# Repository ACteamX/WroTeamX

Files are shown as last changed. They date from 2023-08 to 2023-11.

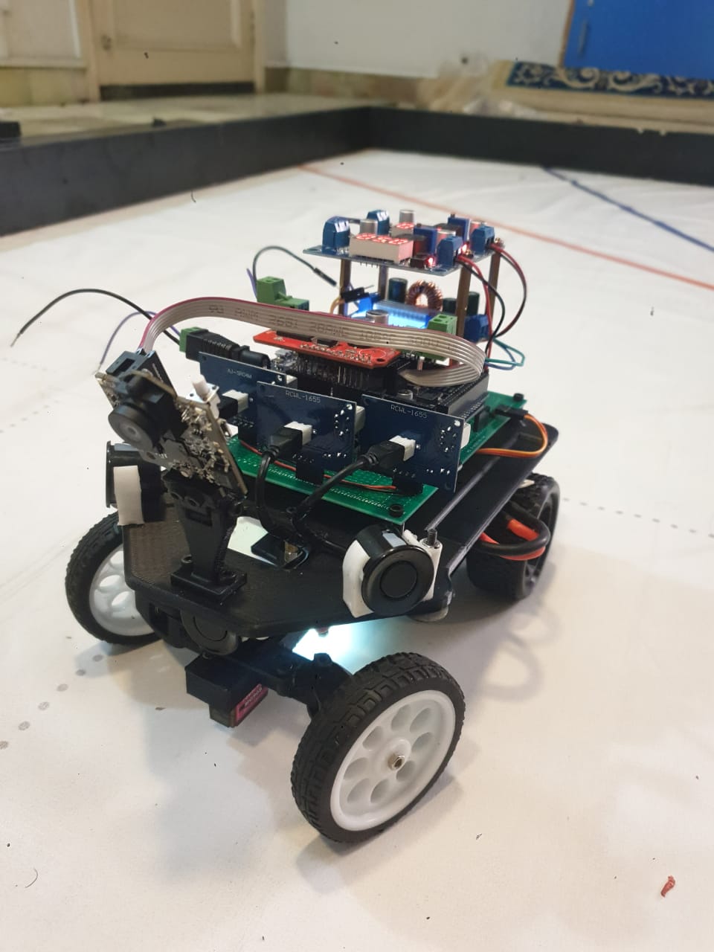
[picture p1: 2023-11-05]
v-photos/new design/wro (11).jpg

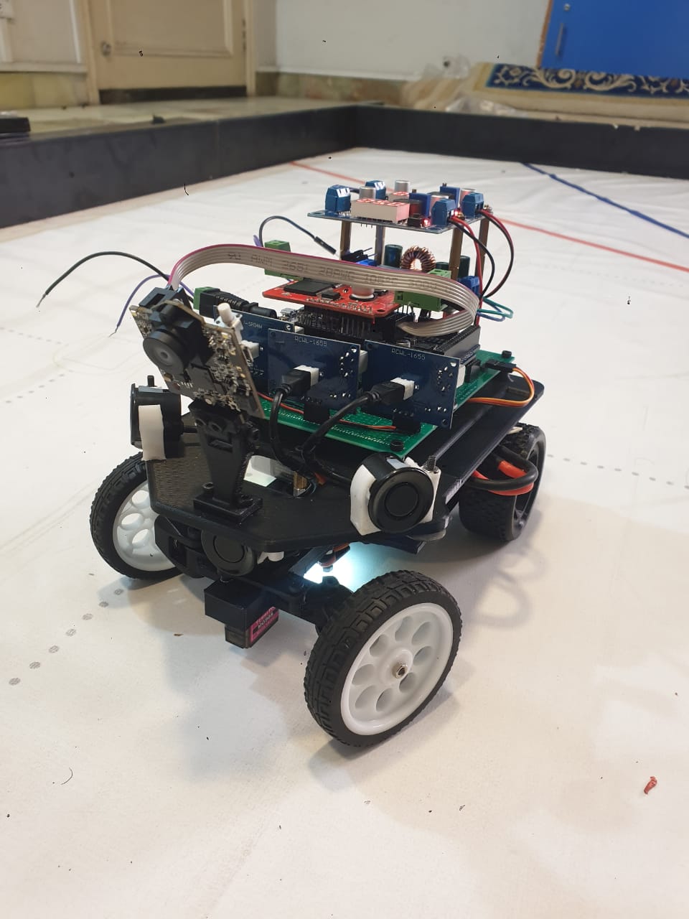
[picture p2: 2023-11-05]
v-photos/new design/wro (13).jpg

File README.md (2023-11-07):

# WroTeamX

This repository contains technical materials for a self-navigating vehicle prototype intended for the WRO Future Engineers event in the 2023 season. Detailed insights into each subcomponent of the robotic system can be explored in the README.md files located within respective folders.

### Contents:

- **Build:** Detailed documentation focusing on our chassis design and the rationale behind the chosen materials.
- 
- **Electrical:** Schematic diagrams illustrating the interconnections among various electromechanical components, including datasheets and explanations for component selection.
- 
- **Models:** Files used by 3D printers to fabricate the vehicle's components.
- 
- **t-Photos:** Folder containing team photos.
- 
- **v-Photos:** Images of the robot.
- 
- **Src:** Software code responsible for controlling all the components programmed for the competition.
- 
- **Schemes:** Documentation and diagrams elucidating our approach to solving the competition's challenges.
- 
- **Video:** Includes the 'video.md' file containing the link to a video demonstrating the vehicle's operational abilities.

### Requirements:

This project meets the following requirements specified by the WRO Future Engineers event:
**Mobility Management** is found in electrical and models

**Power and Sense Management** is found in schemes.

***Components List** The list of all components is in schemes as well.

**Obstacle Management** and coding files are found in src.

**Pictures**  Team and Vehicle is found in photos.

**Performance Videos** are in video folder.

**Engineering Factor** is found in models.

### Introduction:
AcTeamX by mechabotix is a team of high school students from Aitchison College Lahore Pakistan. We have been working on our robot since june .
We have won the National round and then qualified for international round. We are working hard to get the position in the International round as well.
Instead of buying OFF THE SHELF materials for the design of our car , we have designed our car by ourselves . We made 3d models then got the print of the car .
In the National round , we made a design and used that oe but that was really big car and we afraid that it may hit the obstacles so we changed the design making it smaller one .
As far as the electrical components are concerned , we have used pixy camera for detecting the obstacles and used sonar sensors for avoiding the walls .

### Aim of participation:

**Skills Enhancement:** Develop expertise in robotics, coding, and problem-solving.

**Innovative Solutions:** Foster creativity in tackling challenges through innovative robotics solutions.

**Team Collaboration:** Strengthen teamwork and communication skills within a competitive environment.

**Global Engagement:** Engage and learn from a diverse global community of robotics enthusiasts.

**Critical Thinking:** Enhance critical thinking and problem-solving abilities in real-world scenarios.

**Competition Experience:** Learn to perform under pressure and manage time effectively in a competitive setting.

**STEM Advocacy:** Promote STEM education and interest in robotics and technology.

**Personal Growth:** Encourage individual growth and confidence through overcoming challenges.

**Technology Exposure:** Stay updated on cutting-edge technology trends in robotics and automation.

**NEW CAR VS OLD CAR**
NEW DESIGN) sidetiltright

**DIFFERENCES**

**1.DESIGN**

  **OLD CAR** We made a bigger car in National round for WRO and we have won too but we felt that it is too big to cross obstacles .
We were afraid that it might hit the obstacles with its big design.the dimensions of our old car are 26x19.8x25cm length width and height and the weight of this car was 1490g. Our old car was very close to maximum dimensions are weight allowed for the car so we had a concern of disqualification as well. We used thick 3D printed wheels as well in our old car. We used some 3d printed parts and used some PVC sheets for the upper base of our car , it was 3 storeys car which was very big so we decided to change it.

**NEW CAR** In the new car , we made a new design making it small and fast. We have made so many changes in our design. The new dimensions are very less than the dimensions of our prevoius robot.This Robot is fast and we have have made design flexible that we can easily change the components when required. 

**ELECTRONICS components**

**Old Car** In the old car, we used the raspberry pi and connected it with arduino by sending signals to arduino from pi and we used CV2 library for detecting the obstacles.We used Power banks to power our arduino and raspberry pi. Also, we used only two buck and boost convertors for powering the main motor , sensors and servo motor. This thing disturbed us so much that whenever servo motor moves that it produces noise in the sensors and readings fluatuates.So, we have faced so many issues in our old robot .

**New Car** In the new car, we have used Arduino due and for obstacle detetction we have used the pixy camera as it is easy to use and train models. For reducing noise, we have now used two batteries and 1 battery is connected in parallel with one buck convertor(giving 5V to sensors) and one buck-boost convertor(giving power to drive motor and Arduino Due), the other battery is connected with a convertor separately which is giving 5V to servo motor. Also for making the output smooth , we have used some capacitors in parallel fashion to all our components like sensors, motors etc.
So, these are the thing which we missing in our prevois Robot.

ALSO,
we have used vero board and designed the circuit on it as it looks professional and accurate , it was not present in old robot.

vero board
vero board

**Note**

****An important thing to note that is that we tried to use MPU920 and RGB color sensor for getting the best output but the sensors available in Pakistan are too noisy to use, we tried so many times for getting accurate readings but failed, with MPU920 we used kalman filter and it was working fine but when we tried to put it in our car then the readings started fluctuating and same faced same thing with RGB color sensor, so we tried to rely on encoder motor and pixy camera for making U-turn.
we have uploaded our all codes in the SRC file.**

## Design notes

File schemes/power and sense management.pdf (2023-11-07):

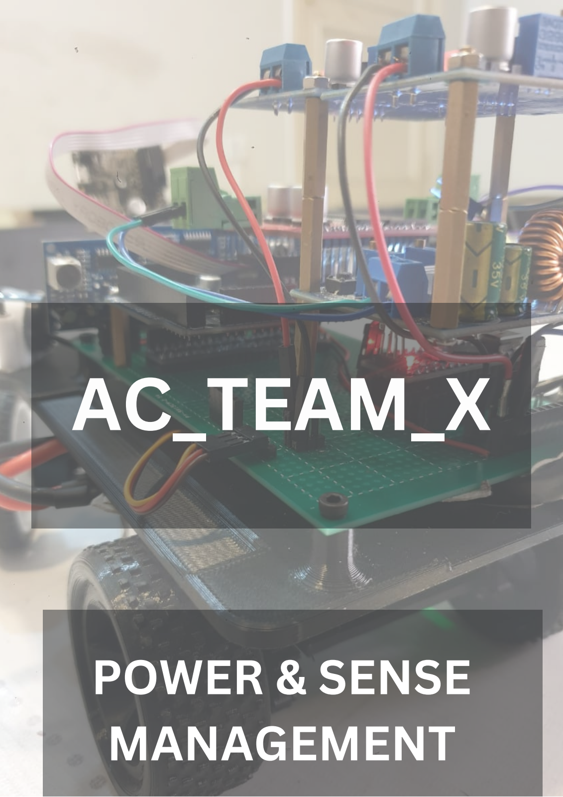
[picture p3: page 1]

AC

_

# TEAM

_

X

# POWER & SENSE MANAGEMENT

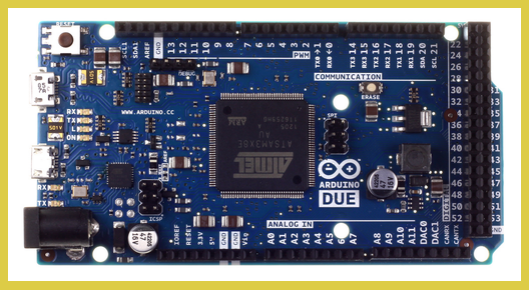
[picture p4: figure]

ARDUINO
DUE

1.

### Instead of using Arduino mega, we have preferred using Arduino Due because of its performance. The RAM and ROM of Arduino

Due is way ahead than Arduino mega .

### The processor of due is also good than Arduino mega . So using Arduino due will give

us a good result.

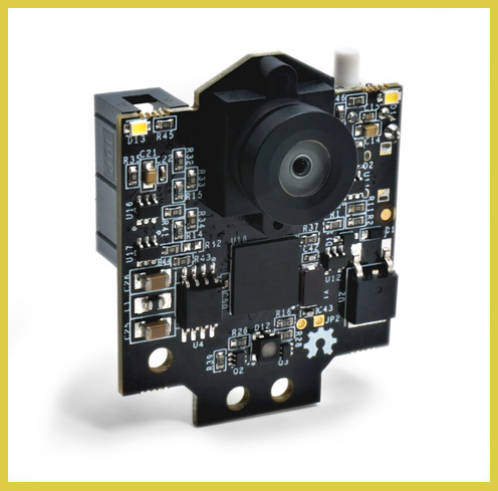
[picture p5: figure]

2.

Pixy Camera, is a compact and versatile vision system primarily used for object recognition and tracking in robotics and automation. Its primary function revolves around efficient object detection and recognition, making it a popular choice for obstacle detection applications . The best thing about pixy is that we can train the models easily and it is a flexible camera . We are detecting green and red colors and sending signal to Arduino . We may use it for detecting blue color and making a U-turn.

### PIXY CAMERA

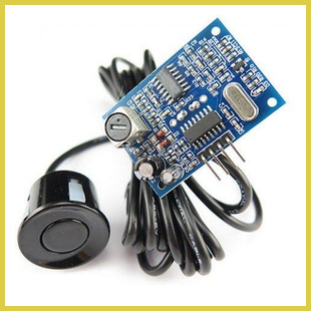
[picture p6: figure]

7.

JSN SR04T
Water Proof
Ultrasonic
Sensor

8

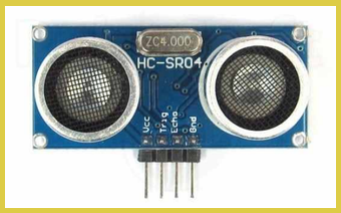
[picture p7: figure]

If necessary , we will use this sonar sensor for our critical turns like where the distance is less than 10cm and we have to avoid the robot from hitting walls . The JSON sonar can’t measure distance below 20cm. So, after testing we will final whether or not we are using the simple sonar sensors .

HC-SR04
Ultrasonic
Sensor

"Jason Waterproof Sonar Sensors" are cutting-edge sensors engineered for obstacle avoidance in autonomous vehicles, renowned for their precision and reliability. These sensors, utilizing sonar technology, offer accurate distance measurement and object detection. Resilient and durable, they ensure consistent and precise readings in varied conditions. We are using 3 of these sensors and we have made a sensor holder too .

# SENSORS AND BOARD

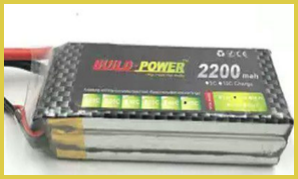
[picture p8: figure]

### 9. We are using one 2200mAh battery and one 1300mAh

battery in our robot .
we faced so many issues of servo motor noise so we are giving power to our servo motor with a separate lipo battery now. The big lipo battery is dedicated for our drive motor , arduino due and all the sensors .

Lipo
Battery

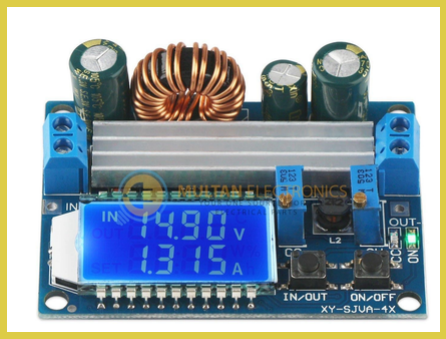
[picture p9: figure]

Buck
Boost
Converter
4A
Module
With LCD
Display

11.
We are using a 4A buck-boost convertor with LCD display for our drive motor and Arduino Due.
It is amazing convertor as we can run our motor at high and low speeds whenever it is required. Also, we are giving 7-12V to Arduino due. If we want to run our at the fastest speed then we will increase the voltage to 15V and give power to Arduino separately with other buck convertor.

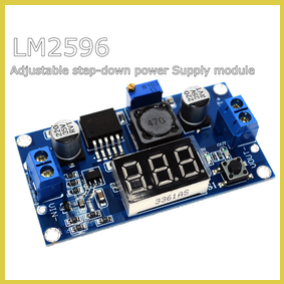
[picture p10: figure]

12.

LM2596
Step Down
buck
convertor

We are using LM2596 Step Down buck convertor to power our sensors and servo motor . We are using 2 convertors , 1 for servo alone and one for sensors . We have connected our one buck convertor to the main battery and used parallel connections with 4A buck-boost convertor , so two convertors and connected to one battery and our third buck convertor is connected to a separate battery for servo motor for reducing noise.

# Arduino Due and Logic Level Shifter

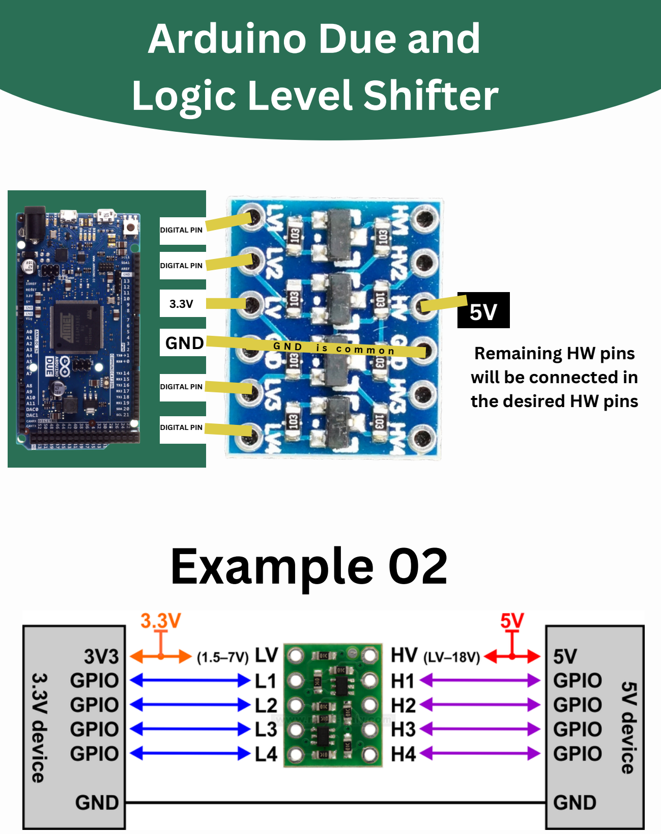
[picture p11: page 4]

## GND

DIGITAL PIN

DIGITAL PIN

3.3V

DIGITAL PIN

DIGITAL PIN

G N D i s c o m m o n

5V

## Remaining HW pins will be connected in the desired HW pins

# Example 02

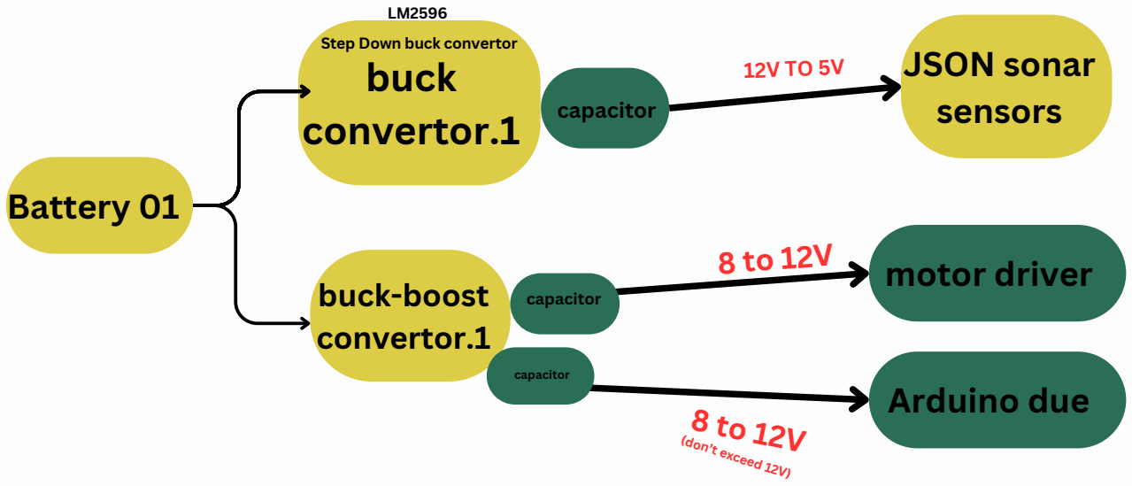
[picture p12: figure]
Battery 01; buck convertor.1; buck-boost convertor.1; JSON sonar sensors; motor driver; Arduino due; (don’t exceed 12V); Step Down buck convertor; capacitor

## Battery 02

## buck convertor.2

12V TO 5V

# 1.Parallel power to both convertors from one battery

AT FIRST , we have used only one battery for all the components and using buck boost for sensors and motors but then we faced too much noise in sonar sensors due to servo motor movements so we have used one separate battery for servo motor.

LM2596
Step Down buck convertor | SERVO

# MOTOR

# MAKING OUTPUT SMOOTH

we have used some capacitors at the output of every buck or
boost convertor for making the output smooth and ensuring there is no external noise , if there is then capacitors can resolve it.Capacitors have the ability to smooth out electrical signals when placed between a power source (such as a battery) and sensors or electronic components. This smoothing effect is primarily due to the capacitor's ability to store and release electrical energy.

capacitor

# note that GND is common of the components

## 2. separate power to servo motor

# Schematics 1.0

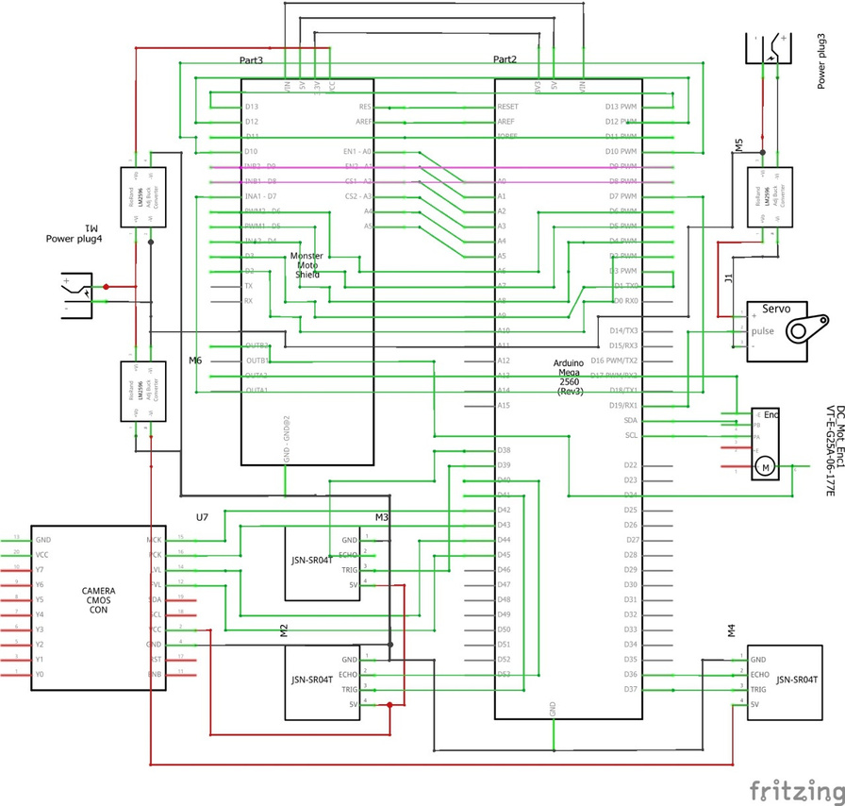
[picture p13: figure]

# Schematics 1.1

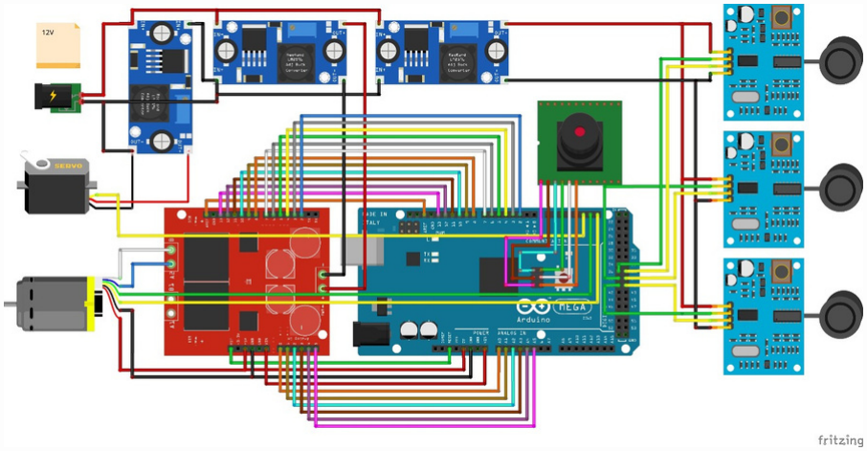
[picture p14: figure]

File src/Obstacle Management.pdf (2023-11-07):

# Obstacle Management

Avoiding obstacles

In our code, pixy returns the center of the obstacle it’s seeing, and Arduino compares the obstacle’s center to the robot’s center. This comparison tells us whether the obstacle is on the left side of the robot or on the right side of the robot. Four cases arise in this way:

- Object is on the left side of the robot:
- Red Obstacle: Steer less (turn at small angle)
- Green Obstacle: Steer More (turn at greater angle)
- Object is on the right side of the robot:
- Red Obstacle: Steer More (turn at greater angle)
- Green Obstacle: Steer less (turn at small angle)

Avoiding wall hit:

While avoiding obstacle robot sometimes steer a lot and end up hitting the wall as it is not in “stayStraight” subroutine. To avoid this, we have utilized left and right sensors. If distance of any of these sensors is less than 22 (as our sensors give minimum value of 19,20) we’ll steer in the opposite direction. In this way we will avoid hitting the wall.

Taking corner turn:

For corner turn, we are only using front sensor and Pixy2 camera. We say it a corner if pixy is not detecting an obstacle and front sensor gives distance between 70 and 50 cm as these are the max and min distance values for the corner turn, respectively.

After detecting a corner turn, we compare distance of left and right sensors and steer on the side with greater distance.

Handling Stop and Turning from red obstacles:

We are using encoder motor which gives us no of pulses that the motor takes as it covers distance. By hit and trial we found that our motor takes 28,000 pulse to complete 7 sections of the arena. We have utilized this information to stop the robot as well as to return on seeing red obstacle in the 2

nd lap.

Both logics are explained as follows:

Stopping after 3 laps:

- Arduino keeps on monitoring pulses from the motor.

- As soon as pulse count reaches 28,000, we know that we are in the end or middle of section 7 and need to cross the 8

th section, we start monitoring front sensor distance.
- If the front sensor sees a distance greater than 150 cm and less than 180 cm, we know that we have turned 90 degrees because there is no other way, where front distance can be greater than 150 cm. In this way our robot will always stop in the middle of the first half of section 1.
- In case there is an obstacle in front of the robot, and it cannot see a distance between 150 and 180 cm, robot will automatically stop before 34,000 pulses. In this scenario, robot will stop in the middle of second half of the first section.

Taking U turn on seeing red obstacle in the 2

nd lap:

To take U turn on red obstacle in the 7th section of second lap, we complete one lap by completing 28,000 pulses and then looking for front distance as described in the obstacle avoidance section of the document, then we reset the pulse count to zero and start counting for next lap. Next actions are bulleted down:

- Keep on moving until pulse count reaches 28,000.
- Stop the car for 1 sec.
- Make the car straight if it has stopped at an angle.
- Look for obstacle color.
- If it’s green, break the loop and keep going.
- Otherwise, avoid the obstacle using the “obstacleTurn” subroutine.
- Keep the car moving for 0.5 seconds to ensure that it has crossed the obstacle.
- After that Steer leftwards at a larger angle and keep going for 0.8 seconds, in this time obstacle can turn 180 degrees.
- Reset the pulse counter, up count the lap counter and keep going until it completes 28,000 pulses.

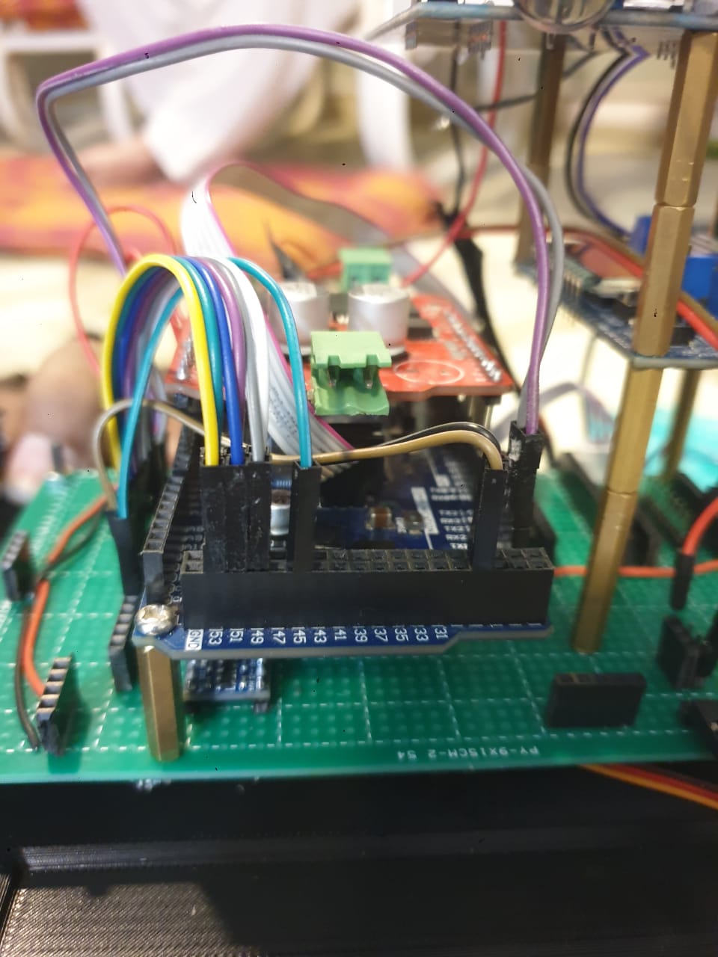
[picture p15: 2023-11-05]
v-photos/new design/wro (1).jpg

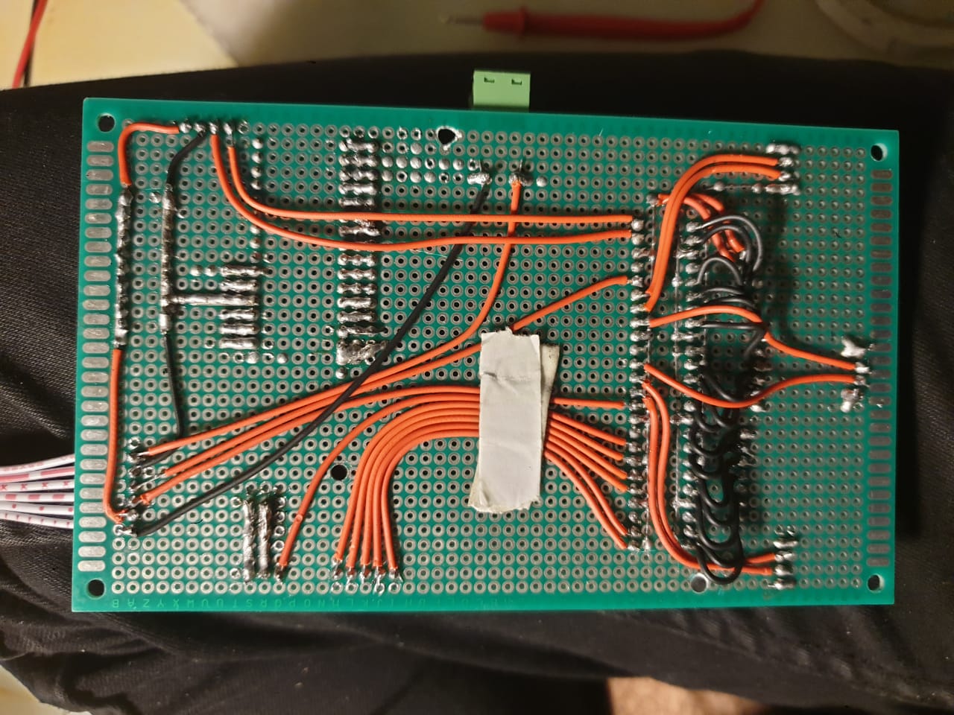
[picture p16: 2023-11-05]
v-photos/new design/wro (5).jpg

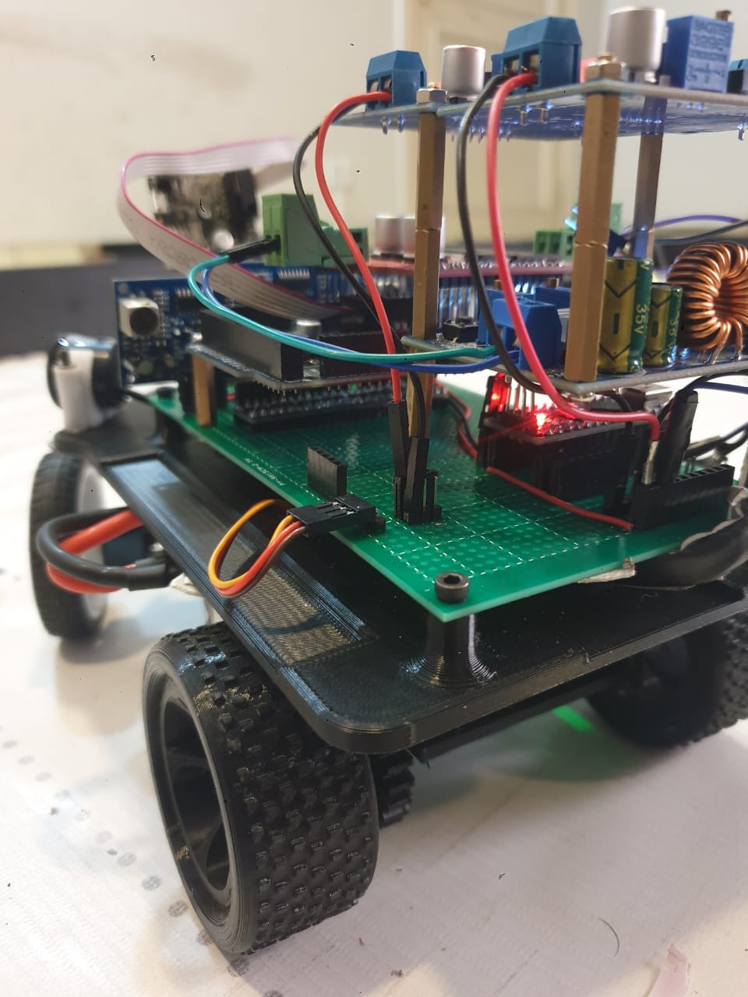
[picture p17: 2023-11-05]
v-photos/new design/wro (8).jpg

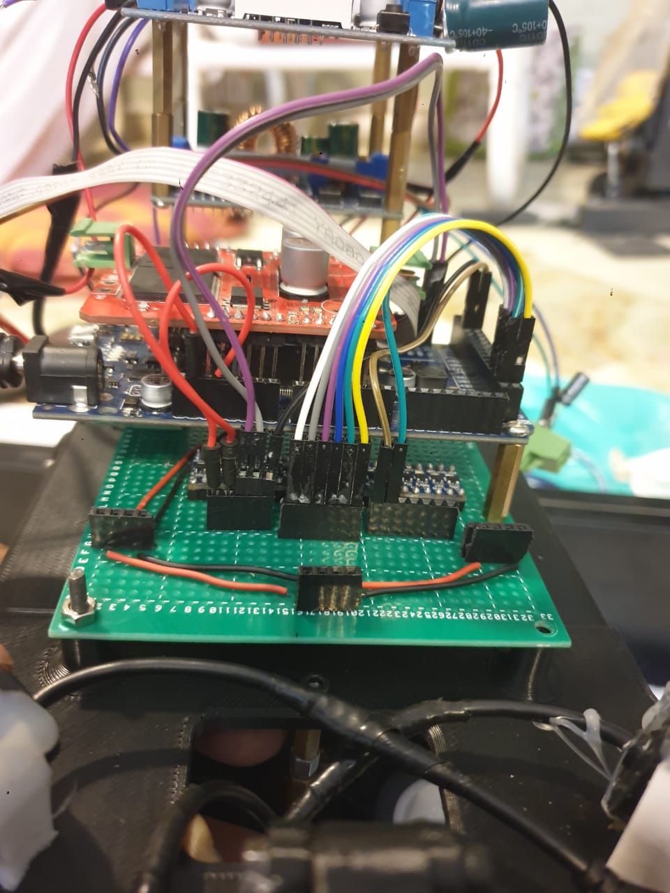
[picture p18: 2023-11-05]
v-photos/new design/wro (3).jpg

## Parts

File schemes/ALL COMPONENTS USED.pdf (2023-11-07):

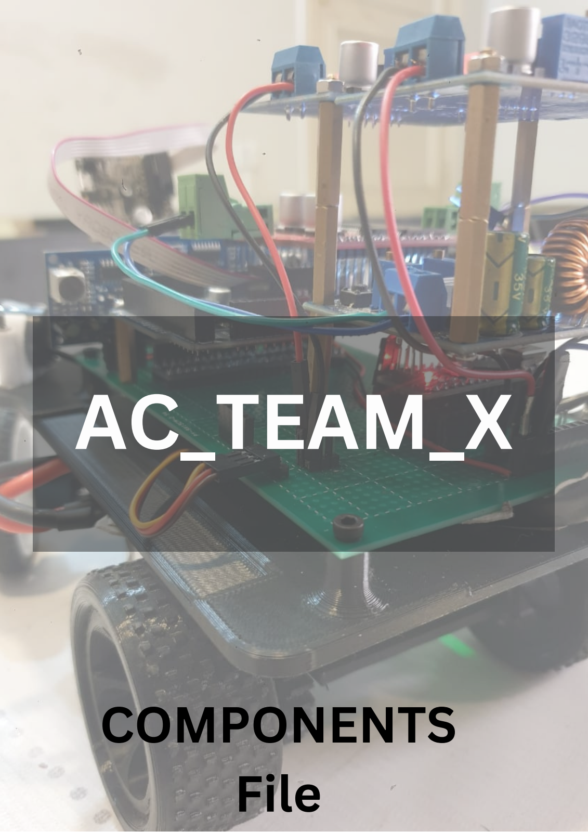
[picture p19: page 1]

AC

_

# TEAM

_

X

# COMPONENTS File

# Components Used

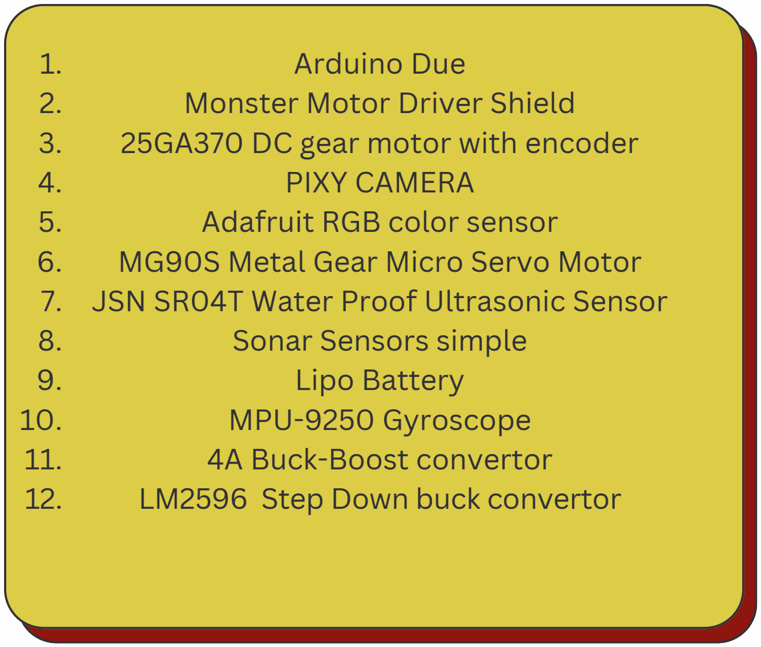
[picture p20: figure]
Arduino Due Monster Motor Driver Shield 25GA370 DC gear motor with encoder PIXY CAMERA Adafruit RGB color sensor MG90S Metal Gear Micro Servo Motor JSN SR04T Water Proof Ultrasonic Sensor Sonar Sensors simple Lipo Battery MPU-9250 Gyroscope 4A Buck-Boost convertor LM2596 Step Down buck convertor

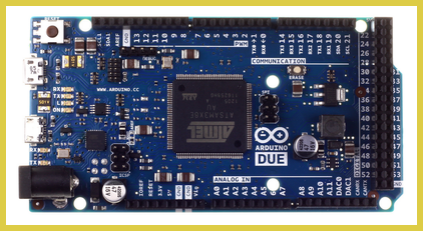
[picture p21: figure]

ARDUINO
DUE

1.

### Instead of using Arduino mega, we have preferred using Arduino Due because of its performance. The RAM and ROM of Arduino

Due is way ahead than Arduino mega .

### The processor of due is also good than Arduino mega . So using Arduino due will give

us a good result.

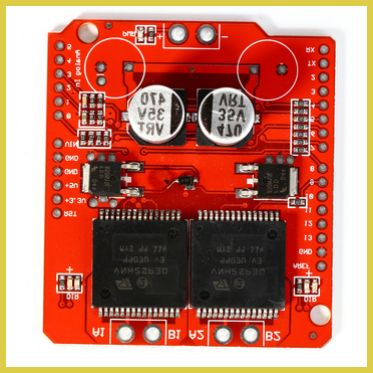
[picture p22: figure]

(VNH2SP30
chip)

2.
We are using VNH2SP30 chip Monster Motor driver shield and pasting it over Arduino Due .
The reason of using VNH is that it is compact and does not occupy much space and also it’s performance is far better than other motor drivers. It has vast applications and very easy to use above all it has no heating effects over large values of current.

Monster Motor Driver Shield

3.
As we know that, Arduino Due gives the 3.3V logic level output so have to use logic level shifters with Arduino Due . Logic level shifters are converting 3.3V of Arduino due to 5V logics required for sensors and motors.
We have connected the digital pins of Arduino Due to LV side of logic level and connected HV side to sensors and motors and making ground common .

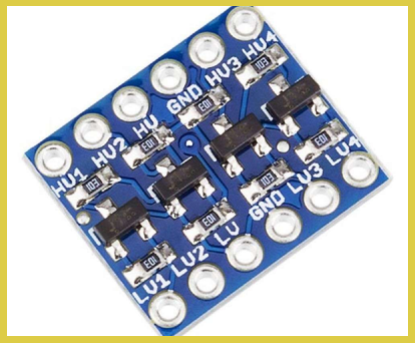
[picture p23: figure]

Bi- directional

Logic Level
shifter


4.

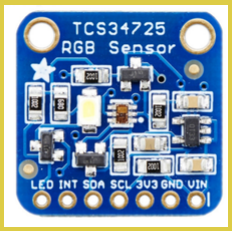
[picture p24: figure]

We have used Adafruit RGB color sensor for detecting orange and blue lines. we are detecting the blue and orange lines for making corner turn and for making a U-

turn . Adafruit
RGB
color
sensor

5.

Pixy Camera, is a compact and versatile vision system primarily used for object recognition and tracking in robotics and automation. Its primary function revolves around efficient object detection and recognition, making it a popular choice for obstacle detection applications . The best thing about pixy is that we can train the models easily and it is a flexible camera . We are detecting green and red colors and sending signal to Arduino . We may use it for detecting blue color and making a U-turn.

WE HAVE BACKUP PLAN IF OUR COLOR SENSOR DIDN’T WORK DURING COMPETITION

PIXY
CAMERA

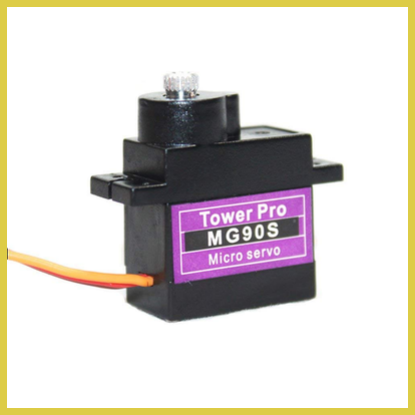
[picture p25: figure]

MG90S
Metal
Gear
Micro
Servo
Motor

6.

### For the steering control, we have used metal gear micro servo motor mg90s. We ae moving

our robot left and right using this servo motor .

### we have made specially designed servo holder in our car that we can replace it easily if it is

damaged.It is an Analog Servo motor.


7.

JSN SR04T
Water Proof
Ultrasonic
Sensor

8

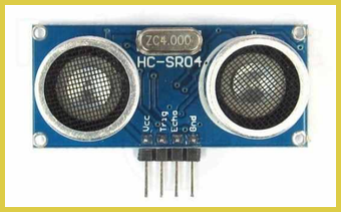
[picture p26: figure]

If necessary , we will use this sonar sensor for our critical turns like where the distance is less than 10cm and we have to avoid the robot from hitting walls . The JSON sonar can’t measure distance below 20cm. So, after testing we will final whether or not we are using the simple sonar sensors .

HC-SR04
Ultrasonic
Sensor


9.


MPU9250
GY-9250 9
Axis
Gyroscope

10.

We are using one 2200mAh battery and one 1300mAh battery in our robot .
we faced so many issues of servo motor noise so we are giving power to our servo motor with a separate lipo battery now. The big lipo battery is dedicated for our drive motor , arduino due and all the sensors .

### not using it but we have tried it many times

Lipo
Battery

"Jason Waterproof Sonar Sensors" are cutting-edge sensors engineered for obstacle avoidance in autonomous vehicles, renowned for their precision and reliability. These sensors, utilizing sonar technology, offer accurate distance measurement and object detection. Resilient and durable, they ensure consistent and precise readings in varied conditions. We are using 3 of these sensors and we have made a sensor holder too .

We have tried using the gyroscope in our robot , but the thing is there are not good gyroscopes available in Pakistan, all give inaccurate reading , we tried really hard on it , tried different approaches like kalman filter etc but still it is not working well and giving us some fluctuations


Buck
Boost
Converter
4A
Module
With LCD
Display

12.
We are using a 4A buck-boost convertor with LCD display for our drive motor and Arduino Due.
It is amazing convertor as we can run our motor at high and low speeds whenever it is required. Also, we are giving 7-12V to Arduino due. If we want to run our at the fastest speed then we will increase the voltage to 15V and give power to Arduino separately with other buck convertor.


13.

LM2596
Step Down
buck
convertor

We are using LM2596 Step Down buck convertor to power our sensors and servo motor . We are using 2 convertors , 1 for servo alone and one for sensors . We have connected our one buck convertor to the main battery and used parallel connections with 4A buck-boost convertor , so two convertors and connected to one battery and our third buck convertor is connected to a separate battery for servo motor for reducing noise.

AC


# TEAM

11.

We have used 25GA370 DC gear motor with built-in encoder. The best advantage of this motor is that we don’t need to buy external encoder for pulse count .Operating at 12V, the motor's speed ranges from 280 RPM at 12V, 210 RPM at 9V, to 325 RPM at 14V. This motor can be operated at lower speeds as well .it has 6 pins 2 for motor , 2 encoder +,- and two encoder pulse count signal pins

25GA370 DC
gear motor
with encoder

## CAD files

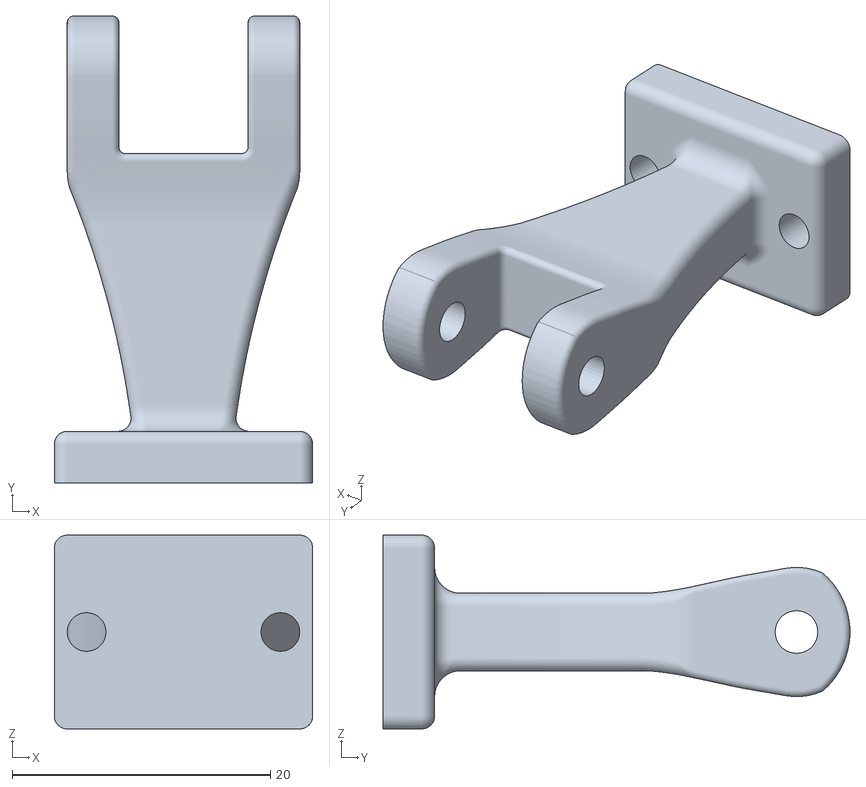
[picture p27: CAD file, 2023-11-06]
models/new versions/STL files/Lower Connector.STL
20.0 x 36.1 x 15.0

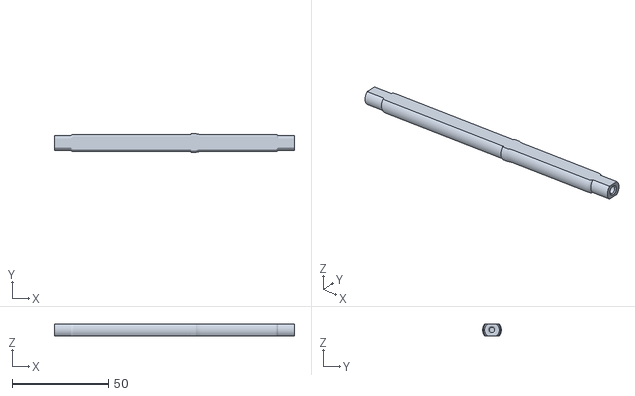
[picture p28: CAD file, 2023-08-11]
Rear_Shaft.stl
125.0 x 9.80 x 6.00

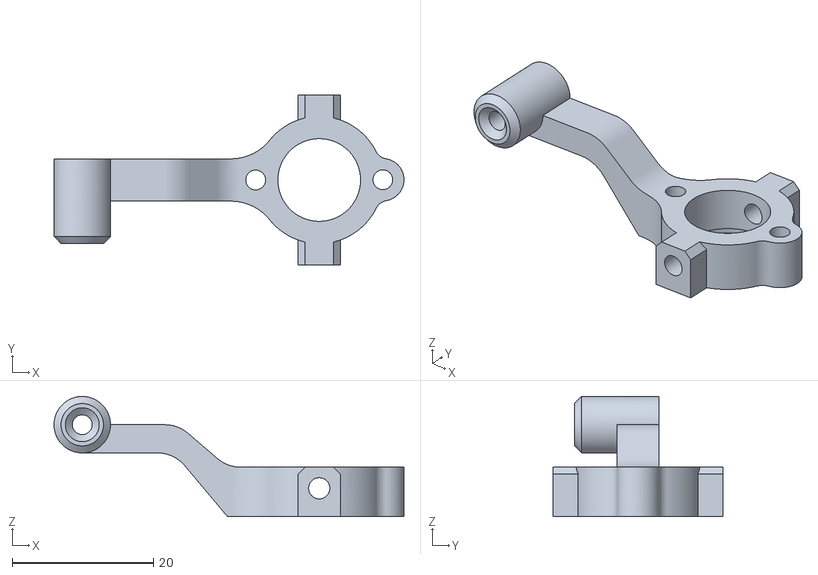
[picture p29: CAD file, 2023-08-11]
Front_HubRight.stl
49.6 x 24.0 x 17.0

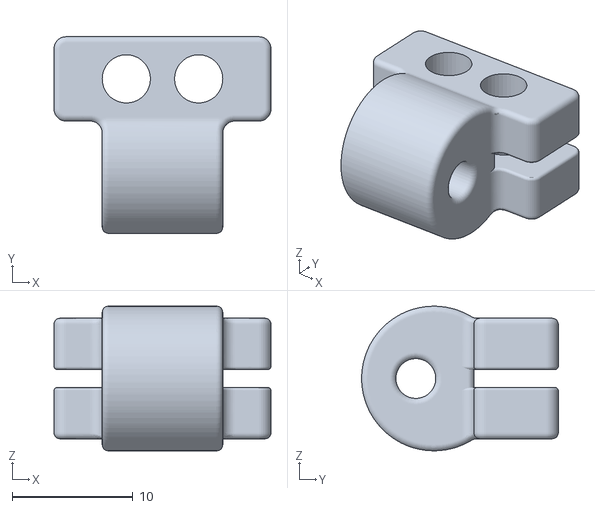
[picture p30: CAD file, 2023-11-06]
models/new versions/STL files/Upper Connector.STL
18.0 x 16.3 x 12.0

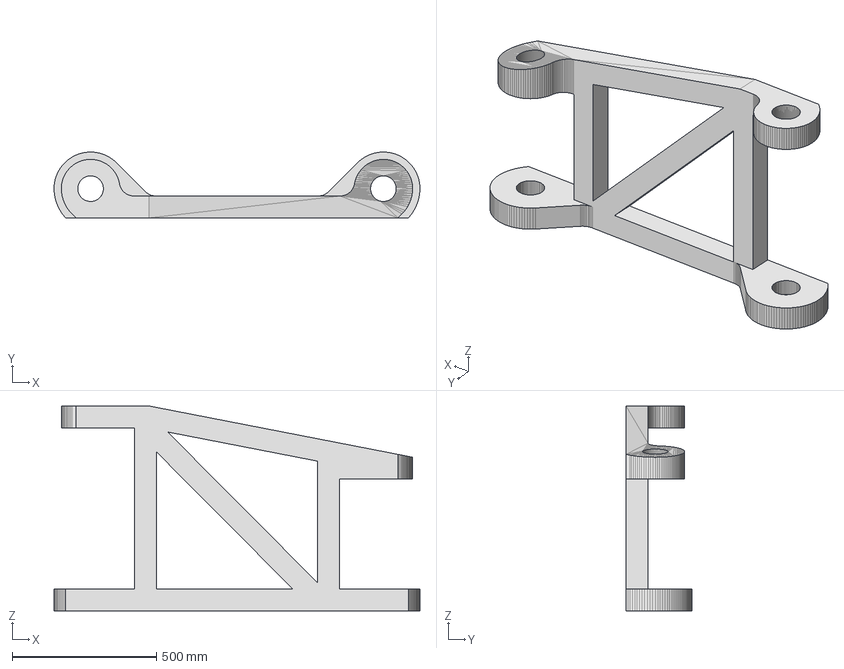
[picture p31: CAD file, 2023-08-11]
front suspensin link rear left.stp
1270.0 x 228.6 x 711.2 mm

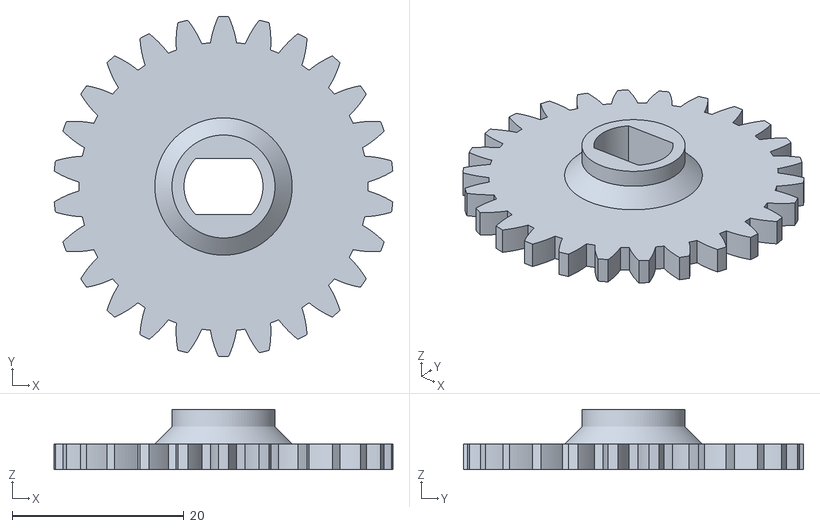
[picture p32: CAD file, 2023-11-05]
models/new versions/STL files/crown_gear.stl
39.5 x 39.6 x 7.00

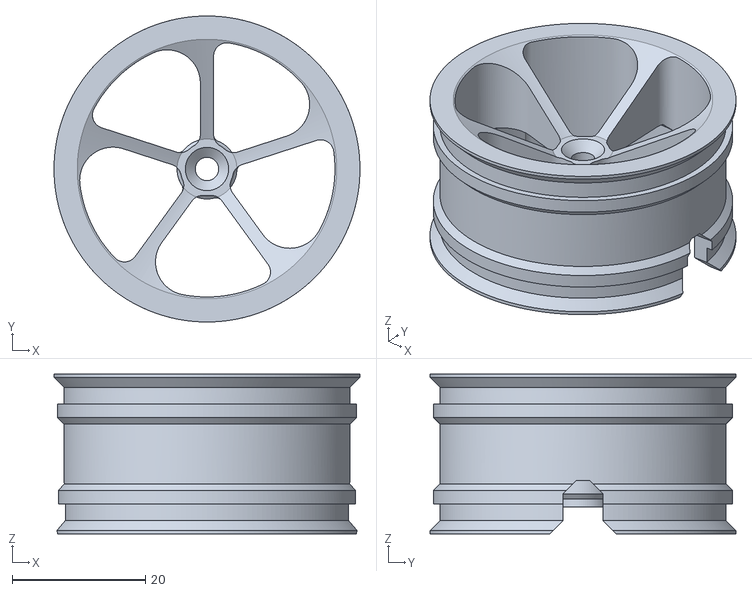
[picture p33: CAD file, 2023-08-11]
Front_Wheel.stl
46.0 x 46.0 x 24.0

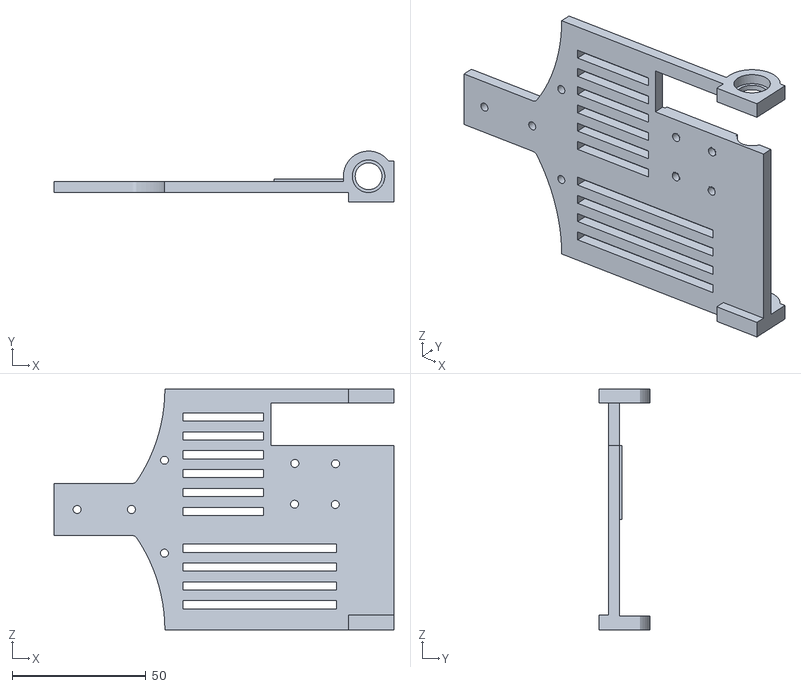
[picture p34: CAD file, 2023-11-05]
models/new versions/STL files/Central Body.stl
127.0 x 19.0 x 90.0

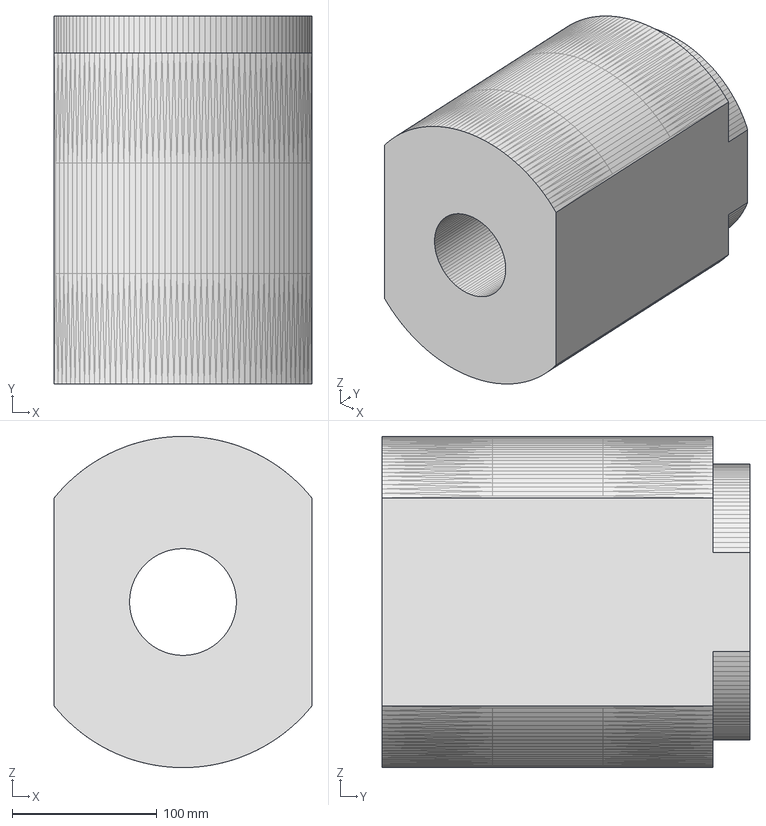
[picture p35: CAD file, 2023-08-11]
front wheel bearing lock.stp
177.8 x 254.0 x 228.6 mm

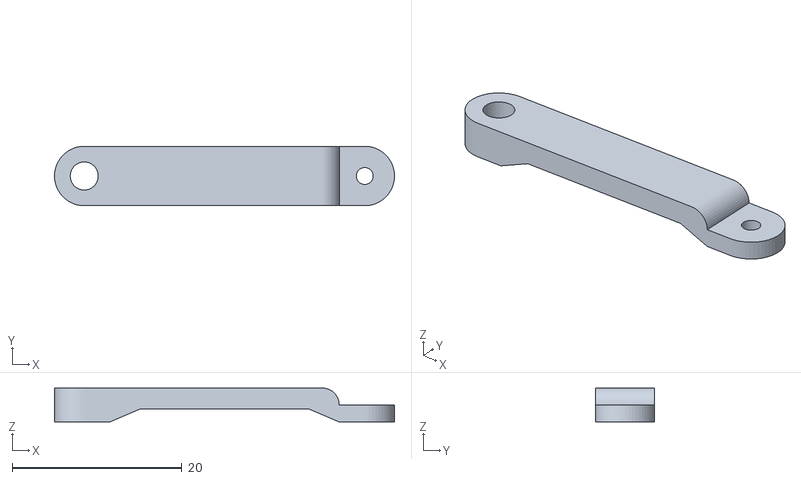
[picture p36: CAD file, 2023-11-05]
models/new versions/STL files/steering link.stl
40.0 x 7.00 x 4.00

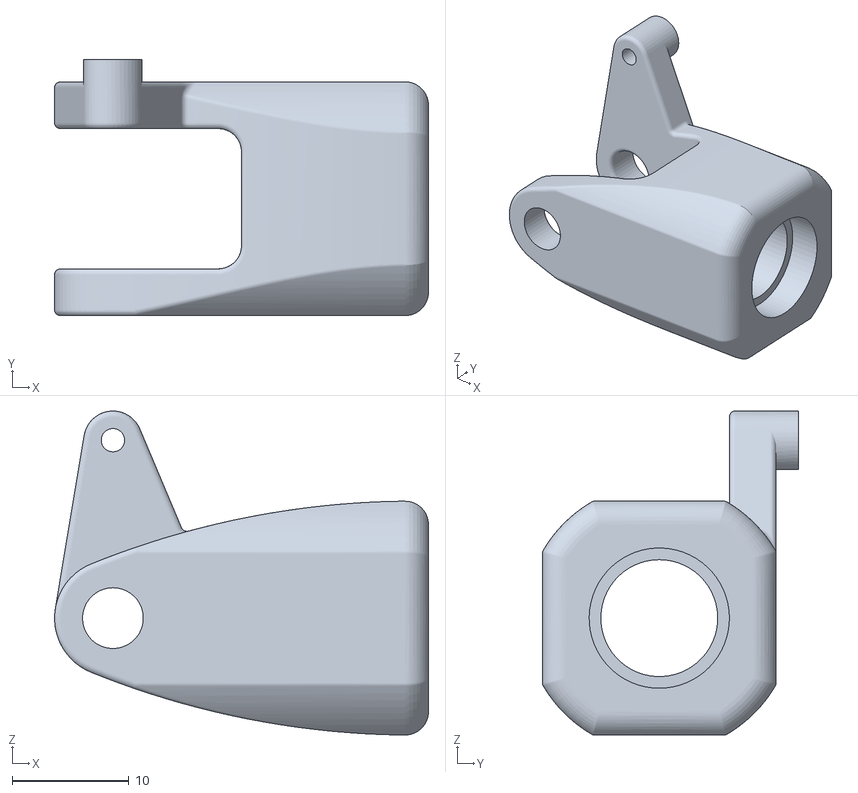
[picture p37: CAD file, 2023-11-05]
models/new versions/STL files/Front Wheel Hub Left and Right.stl
32.0 x 21.9 x 27.7

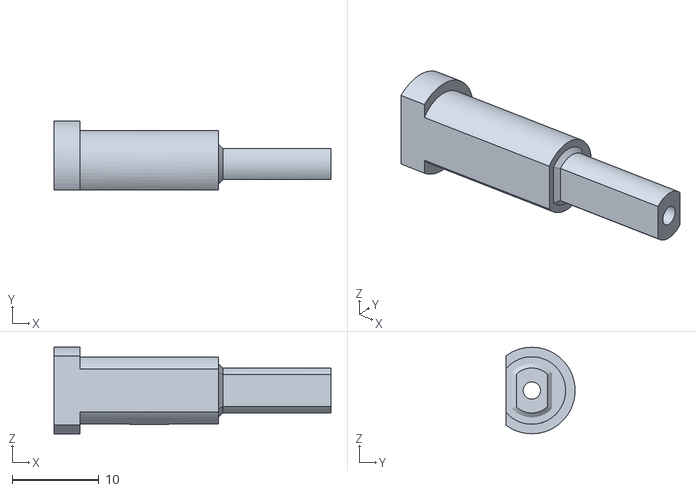
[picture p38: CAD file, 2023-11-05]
models/new versions/STL files/Front Wheel Shaft.stl
32.0 x 8.00 x 10.00

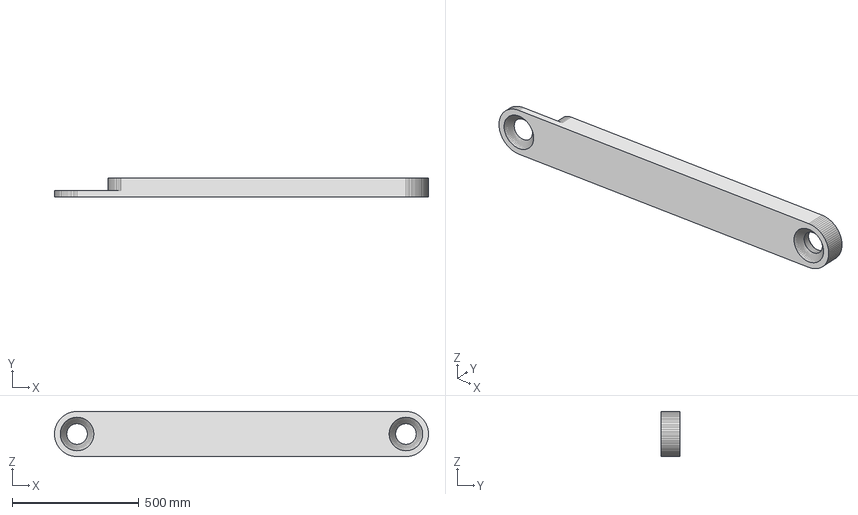
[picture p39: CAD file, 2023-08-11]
steering link.stp
1473.1 x 76.2 x 177.8 mm

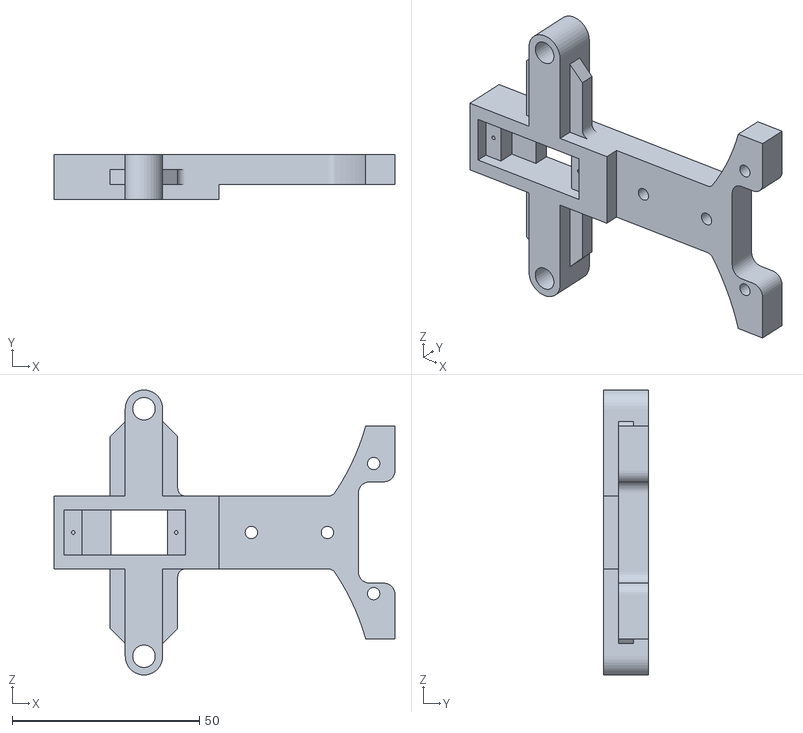
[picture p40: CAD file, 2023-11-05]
models/new versions/STL files/Chasis.stl
90.9 x 12.0 x 76.0

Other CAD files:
Front_HubLeft.stl
models/new versions/STL files/Front Hub Pin.stl
Rear Suspension 1.stp
Gear 3.stp
Chassis.stl
Front Suspension Link upper left.ipt
Front_HubCap.stl
Front_HubMount.stl
Front_SuspensionBottomLeft.stl
Front_SuspensionBottomRight.stl
Front_SuspensionUpperLeft.stl
Front_SuspensionUpperRight.stl
Front_WheelLock.stl
Gear 2.ipt
Gear 2.stp
Gear 3.ipt
Hurdle.ipt
Hurdle.stp
Part1.stl
Part2 - Copy.stl
Part2.stl
Part3.stl
Rear Suspension Upper Plate.stp
Rear Suspension.stp
RearSuspension_Hub.stl
Rear_Wheel.stl
SteeringLink.stl
crown gear.ipt
crown gear.stp
front hub cap.ipt
front hub cap.stp
front hub mount.ipt
front hub mount.stp
front suspenion link rear right.ipt
front suspenion link rear right.stp
front suspensin link rear left.ipt
front suspension link upper right.dwg
front suspension link upper right.ipt
front suspention hub left.ipt
front suspention hub right.ipt
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

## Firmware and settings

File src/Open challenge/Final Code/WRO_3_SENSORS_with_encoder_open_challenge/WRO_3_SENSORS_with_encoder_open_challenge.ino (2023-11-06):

#include <Servo.h>

const int TRIGGER_PIN_FRONT = 44;  // Front sonar sensor trigger pin
const int ECHO_PIN_FRONT = 45;     // Front sonar sensor echo pin

const int TRIGGER_PIN_LEFT = 46;  // Left sonar sensor trigger pin
const int ECHO_PIN_LEFT =47;     // Left sonar sensor echo pin

const int TRIGGER_PIN_RIGHT = 42;  // Right sonar sensor trigger pin
const int ECHO_PIN_RIGHT = 43;     // Right sonar sensor echo pin

const int motor1 = 4;
const int motor2 = 9;
const int pwm = 6;
//encoder
const int ENCA = 27;  // Encoder pulse input A
const int ENCB = 26;  // Encoder pulse input B

Servo steeringServo;

const int forwardSpeed = 150;  // Adjust this value for the desired forward speed
const int turnSpeed = 130;     // Adjust this value for the desired turn speed

volatile long posi = 0;  // Use long to accommodate larger position values

// Stop the car if pulse count is greater than 34000
int lapCount = 1;
const int totalLaps = 3;  // Set the total number of laps

void setup() {
  Serial.begin(9600);
  steeringServo.attach(53);

  // Motor
  pinMode(motor1, OUTPUT);
  pinMode(pwm, OUTPUT);
  pinMode(motor2, OUTPUT);

  // Sonar Sensors
  pinMode(TRIGGER_PIN_FRONT, OUTPUT);
  pinMode(ECHO_PIN_FRONT, INPUT);
  pinMode(TRIGGER_PIN_LEFT, OUTPUT);
  pinMode(ECHO_PIN_LEFT, INPUT);
  pinMode(TRIGGER_PIN_RIGHT, OUTPUT);
  pinMode(ECHO_PIN_RIGHT, INPUT);

  // Encoder
  pinMode(ENCA, INPUT);
  pinMode(ENCB, INPUT);
  attachInterrupt(digitalPinToInterrupt(ENCA), readEncoder, RISING);

  Serial.println("Car position calculation using encoder pulses...");
}

void loop() {
  int distanceFront = getDistance(TRIGGER_PIN_FRONT, ECHO_PIN_FRONT);
  int distanceLeft = getDistance(TRIGGER_PIN_LEFT, ECHO_PIN_LEFT);
  int distanceRight = getDistance(TRIGGER_PIN_RIGHT, ECHO_PIN_RIGHT);

  // Print sensor readings
  Serial.print("Front Distance: ");
  Serial.print(distanceFront);
  Serial.print(" cm, Left Distance: ");
  Serial.print(distanceLeft);
  Serial.print(" cm, Right Distance: ");
  Serial.print(distanceRight);
  Serial.print(" cm, Current position: ");
  Serial.println(posi);

  // Your code to check the conditions
  if (posi > 30000 && (distanceFront > 150 && distanceFront < 170)) {
    // Reset encoder position after each lap
    if (lapCount == totalLaps) {
      digitalWrite(motor1, LOW);
      digitalWrite(motor2, LOW);
      analogWrite(pwm, 0);
      Serial.println("All laps completed. Stopping the car.");
      while (true)
        ;  // This will halt the program and effectively stop the car
    } else {
      // Increment the lap count
      lapCount++;
      posi = 0;
    }
  }



  // Implement obstacle avoidance based on sensor readings
  if (distanceFront >= 0 && distanceFront <= 50) {
    // Obstacle avoidance logic
    if (distanceRight > distanceLeft) {

      steeringServo.write(50);
      moveForward(turnSpeed);
      delay(200);
    } else if (distanceLeft > distanceRight) {

      steeringServo.write(140);
      moveForward(turnSpeed);
      delay(200);
    }
  } 
    // Obstacle avoidance logic when distanceFront is greater than or equal to 40
     if (distanceFront >= 0 && distanceFront >=30){
    if (distanceRight > distanceLeft) {
      steeringServo.write(80);
      moveForward(turnSpeed);
      delay(20);
    }
    if (distanceLeft > distanceRight) {
      steeringServo.write(110);
      moveForward(turnSpeed);
      delay(20);
    }
  }
  //CRITICAL TURN
 if (distanceRight <25) {
      steeringServo.write(110);
      moveForward(turnSpeed);
      delay(10);
    }
    if (distanceLeft <25) {
      steeringServo.write(80);
      moveForward(turnSpeed);
      delay(10);
    }
}

int getDistance(int triggerPin, int echoPin) {
  digitalWrite(triggerPin, LOW);
  delayMicroseconds(2);
  digitalWrite(triggerPin, HIGH);
  delayMicroseconds(15);
  digitalWrite(triggerPin, LOW);

  unsigned long duration = pulseIn(echoPin, HIGH);
  int distance = duration * 0.0343 / 2;
  return distance;
}

void moveForward(int speed) {
  digitalWrite(motor1, HIGH);
  digitalWrite(motor2, LOW);
  analogWrite(pwm, speed);
}
void moveBack(int speed) {
  digitalWrite(motor1, LOW);
  digitalWrite(motor2, HIGH);
  analogWrite(pwm, speed);
}
void readEncoder() {
  int b = digitalRead(ENCB);
  if (b > 0) {
    posi++;
  } else {
    posi--;
  }
}

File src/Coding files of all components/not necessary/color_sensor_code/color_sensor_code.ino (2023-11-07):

// Include libraries

#include <Wire.h>
#include <Adafruit_TCS34725.h>


// Initialize Color Sensor object
// See parameters: https://learn.adafruit.com/adafruit-color-sensors/program-it
Adafruit_TCS34725 tcs = Adafruit_TCS34725(TCS34725_INTEGRATIONTIME_2_4MS, TCS34725_GAIN_60X);


char col, currentCol, prevCol = 'g';
int colCount = -1;

// setup() is executed once when the Arduino starts
void setup() {

  pinMode(A2, OUTPUT);
  pinMode(A3, OUTPUT);

  // Serial communication to output the value in the serial monitor
  Serial.begin(9600);
  Serial.println("Makerblog.at - MuMs Color Sensor");

  // Check whether Color Sensor also reports back
  if (tcs.begin()) {
    // Everything OK
    Serial.println("Sensor found");
  } else {
    // No sensor found. Freeze program at this point
    Serial.println("TCS34725 not found... process stopped!");
    while (1)
      ;  // Stop!
  }
}

// loop() repeats as long as the Arduino is running
void loop() {

  // The sensor returns values for R, G, B, and a clear value
  uint16_t clearcol, red, green, blue;
  float average, r, g, b;
  delay(10);  // Color measurement takes c. 50ms
  tcs.getRawData(&red, &green, &blue, &clearcol);

  // My attempt at color determination for
  // the 5 M&M colors red, green, blue, orange, and yellow

  // Find the average of RGB
  average = (red + green + blue) / 3;
  // Color values by average,
  // all values now move around 1
  r = red / average;
  g = green / average;
  b = blue / average;


  if (r > g && r > b) {
    currentCol = 'r';
    analogWrite(A2, 168);
    analogWrite(A3, 0);
  }
  if (b > r && b > g) {
    currentCol = 'b';
    analogWrite(A2, 0);
    analogWrite(A3, 168);
  }
  if (g > r && g > b) {
    currentCol = 'g';
    analogWrite(A2, 0);
    analogWrite(A3, 0);
  }

  if (currentCol != prevCol) {
    colCount++;
    prevCol = currentCol;
    Serial.println(colCount);
  }
}
